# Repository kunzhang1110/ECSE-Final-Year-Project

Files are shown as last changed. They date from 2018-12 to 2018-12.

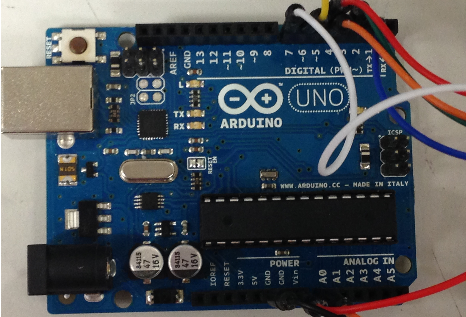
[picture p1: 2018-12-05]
Reports/Poster/Arduino.PNG

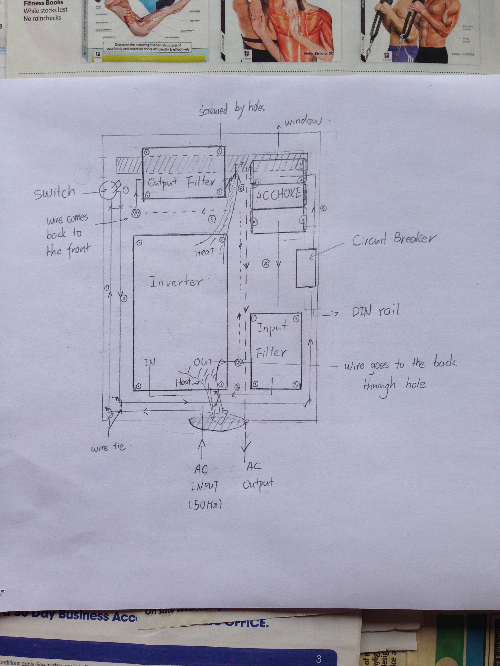
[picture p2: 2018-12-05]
Reports/Final Report/photo1.JPG

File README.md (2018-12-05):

# ECSE-Final-Year-Project
**Monash University**

*Semester 1 and 2, 2013*

## Description
The project is about designing a current-controlled AC-AC inverter and developing programs for controlling and setting this inverter. The inverter is used for motor control and other applications. The innovation of this project involves real-time controlling of the inverter parameters and the control methodology applied. The project also creates fast communication between the inverter and user’s terminals, such as a PC. 

## Environment
* Simulation: Matlab Simulink
* Implementation: Arduino and Atmel PWM controller(AT90PWM3B)
* PCB Board: Altium Designer

## Info
written by Kun Zhang (kunzhang1110@gmail.com)

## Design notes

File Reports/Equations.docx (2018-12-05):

# Power losses

The output current i of the PWM-inverter can be assumed to be sinusoidal with a peak value I_(peak)

i=I_(peak) cos(θ-φ)

where φ is the phase-angle difference between output voltage and current, θ is the phase angle of the voltage.

The conduction loss of one IGBT is

P_(con, 1) =(V_(FI) I_(peak))/(2π)∫_(-π/2+φ)^(π/2+φ) Dcos(θ-φ) dθ

where V_(FI) is the forward voltage of the IGBT and D is the duty cycle

The conduction loss of one bootstrapping diode is

P_(con, 2) =(V_(FD) I_(peak))/(2π)∫_(-π/2+φ)^(π/2+φ) (1-D)cos(θ-φ) dθ

where V_(FD) is the forward voltage of the bootstrapping diode

The duty cycle at a given θ can be obtained by

D=(V_P cosθ+0.5V_(DC))/(V_(DC))

where V_P is the peak of the output phase voltage and VDC is the DC link voltage

Eventually, the conduction losses is given by

P_(con) =P_(con, 1) +P_(con, 2) =(I_(peak))/(2π)(V_(FI) +V_(FD) )+(I_(peak) V_p)/(4V_(DC))(V_(FI) -V_(FD) )cosφ

Assume I_(peak) =20

The switching energy losses L of the IGBTs and diodes can be calculated using the linear equations

L=(E_(sw(on)) +E_(sw(off)) )×i

where, Eon is the switching loss (on) characteristic and Eoff is the switching loss (off) characteristic of the semiconducting devices.

The conduction loss of one IGBT and one diode is

P_(sw) =1/(2π)∫_(-π/2+φ)^(π/2+φ) (E_(sw(on)) +E_(sw(off)) )I_(peak) cos(θ-φ)f_(sw) dθ

where fsw is the switching frequency

By integration, we have

P_(sw) =((E_(sw(on)) +E_(sw(off)) )× f_(sw) I_(peak))/π

The values of the switching loss characteristics can be found in the datasheet

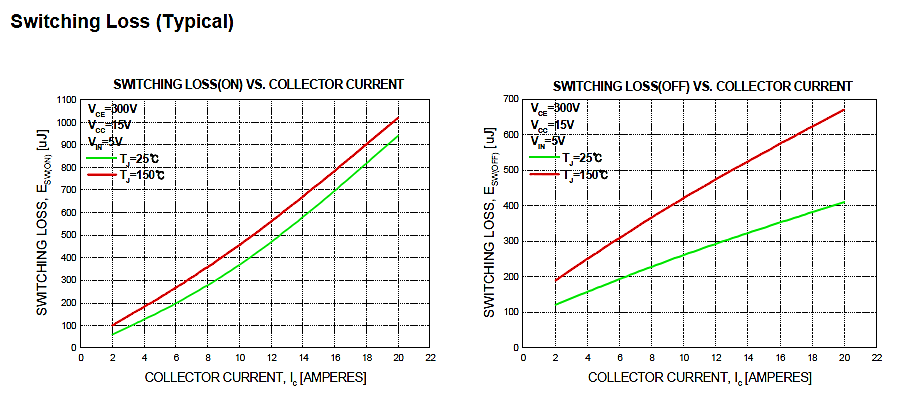
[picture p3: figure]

C=1/(2πfR)=1/(2π×400×18)=22 uF

f_(sw) =1/(t_(loop) *(Count_(Max) -1)+t_(loop_ADC))

where Count_Max is the maximum value of the counter

f_(sw) =1/(t_(loop) *Count_Max)

f_(sin) =f_(sw) *M/(NT)=M/(t_(loop) *Count_Max*NT)

Number of Table Values (NT)=f_(PWM) /f_(MODMAX)

θ=0.0032×108.7×360=125.2

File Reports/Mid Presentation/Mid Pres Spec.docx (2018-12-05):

Hi, my name is Kun Zhang. My final year project is intelligent power-electronics control. This project is an industry-based project, which is offered and supervised by Simplex CNC Systems.

The project is to design a current-controlled AC-AC inverter system which can be used for motor control and other applications. The innovation of the inverter involves real-time controlling of the inverter parameters and the control methodology applied. Also, filters are to be designed and utilised extensively to eliminate possible noises and harmonics.

I am going to talk about AC-AC Conversion methods first, and then I am going to introduce electric protection and filtration used in power electronics systems. Simulations have also been done to simulate the system I designed. At last, I am going to talk about the factory works I’ve been doing for the past seven weeks

Firstly, we need to choose an AC-AC conversion method for our inverter. Three common methods have been considered; they are cycloconverter, DC-link converter and matrix converter.

Cycloconverters synthesize the output waveform from segments of the AC supply. By controlling the switching patterns of the power switches, cycloconverters are able to convert an AC waveform to another AC waveform of a lower frequency. This puts a limit on the usage of cycloconverters as in our application, the frequency desired is 0~500 Hz with the input frequency of 50Hz. So, cycloconverters are not suitable for our design.

Next, lets consider DC-link converters. A DC-link converter converters AC from the mains to DC, and then inverters the DC to an AC with different frequencies. It consists of a rectifier at the supply side and an inverter (usually a voltage-controlled inverter) at the load side. The DC link shown in the middle is a large capacitor. It transmits the DC voltage to the inverter, preventing transients from flowing back to the input and provides some isolation from the utility line. The drawback of DC-link converters is they use large storage capacitors which have short lifetime and are bulky in size

A matrix converter has 9 bi-directional switches (18 transistors) that allow any output phase to be connected to any input phase. The input phases should never be short-circuited and the output currents should not be interrupted. This implies that one and only one bi-directional switch per output phase must be switched on at any instant. The primary advantage is that it reduces the harmonics significantly, hence less complicated filters are needed. However, the implementation and algorithms to control the switches are complex, and the cost is high.

Now, we can compare the three methods. As mentioned earlier, cycloconverters do not meet our frequency requirement, thus they’re not suitable for our design

Matrix converter is excellent insofar as it produces fewer harmonics and requires minimal capacitors and inductors. Yet, in terms of this project, it is not practical because it is too complex and too expensive.

DC-link converter is less efficient and contains considerable harmonics. However, DC-link converters are more feasible due to its low cost and high stability. Additionally, filters can be designed to reduce the harmonics. As a result, DC-link converter is the optimal choice for our application

To implement the conversion methods, we need to find a fitting power module first. A power module is a package of six power switching devices which are connected in bridge configurations. The requirements are shown in the table. The important thing is the switching frequency is 20~30 kilo Hz. This means BJTs cannot be used as they are too slow. GTO and power FETs are fast enough but they cannot stand 35A as required. So our choice is IGBT power modules.

Now, lets jump to electric protection. Electric protection is vital in electrical designs as it protects the system and its operators from faults.

A residual current device disconnects a circuit whenever it detects that the electric current is not balanced between the conductor and the return neutral conductor.

Type A RCDs which can detect full wave AC and pulsating DC residual currents.

Type B RCDs which can detect full wave AC, pulsating DC and pure DC residual

We prefer B as there will be DC current component involved in our application

A circuit breaker is a mechanical switching device, capable of making, carrying and breaking currents under normal circuit conditions.

Residual-current Circuit Breaker (RCCB) is the most common residual current device — detects current imbalance.

On top of that, a Residual current breaker with over-current protection (RCBO) protects the system from over-current. Overcurrent happens occasionally in motor applications, so RCBO is the best protection device in our design. Also, two RCBOs are connected in series, in case one fails

As DC-link converters contain considerable amount of noises, four filters are to be implemented in our design. An ac choke and input EMC filters for the input end and an output EMC filter with an output sine-wave filter for the output end. The total harmonic distortion is expected to be less than 5% for each end.

An ac choke is in essence an inductor which reduces harmonics from the mains. It also reduces commutation notches and limits inrush currents.

(Electromagnetic compatibility) EMC filters reduces the values of dv/dt, thus avoiding sharp changes. The dv/dt filters have cut-off frequency above the switching frequency. These filters also reduce the motor insulation stress. They are designed to be implemented at both input and output end.

Sine-wave filters provide a sinusoidal phase-to-phase motor voltage filtration. They have three effects: they reduce harmonics in the output; they reduce bearing current especially in large motors; Also, they reduce insulation stresses

The system I designed was simulated using Simulinks in MATLAB.

In brief, the DC-link inverter system consists of three blocks, a rectifier rectifies the mains, an inverter converts the DC to desired AC ---- which is fed to a motor. The simulation at this stage is done in open-loop. However, the system will be closed-loop controlled

The rectifier is constructed by six diodes with RC snubbers.

The AC source is configured in a way that it contains some harmonics, which is supposed to be filtered by the input EMC filter and input ac choke.

The rectification schematic also includes the DC-link section which contains an inductor with a large storage capacitor.

The first graph is the rectified voltage after the rectifier and the second graph is the voltage after DC link. It can be seen here that the stabilized output of the rectifier contains mainly DC with moderate distortions. These distortions are further reduced by DC-link.

The voltage is almost DC with a voltage of 150V

The motor simulation assumes the input of the inverter to be a well-rectified DC, which is modelled by a DC source. The three-phase PWM generator is set to generate a 100Hz modulation signal feeding into the inverter. The torque is fed back to the induction motor with a torque-speed characteristic as shown.

The first graph shows the rotor speed and the second graph shows the electromagnetic torque. It can be observed that the rotor speed is constant after 0.18s while the torque stabilizes after the same period of time. The rotor speed is around 180 rad/s (57Hz) because the slip of the induction motor was set to 0.5.

This is an industry-based project, so a considerable amount of works were done in factory. The factory works include assembling cabinets, wiring, device installation and assembling PCs. The cabinets are designed to hold the inverters and the filters. Rivets had to be punched into the metal plates first so that the they could assembled by screws. Once the cabinets were assembled, some model devices were installed in them. This was done by drilling holes to the metal plates of the cabinets and attached the model devices to the plate using's screws via those holes. Then, proper wiring paths were designed and the devices were wired accordingly. In addition, I also learnt and assembled a PC in the factory.

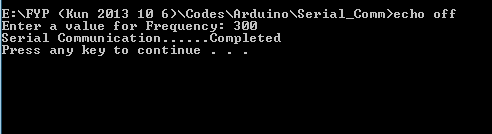
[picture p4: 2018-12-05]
Reports/Poster/BAT_Program.PNG

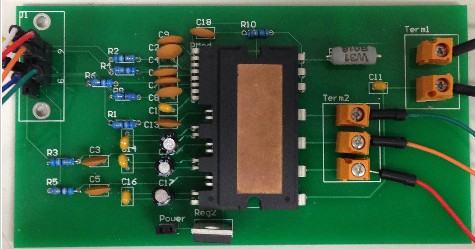
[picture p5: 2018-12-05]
Reports/Poster/PCBBoard.PNG

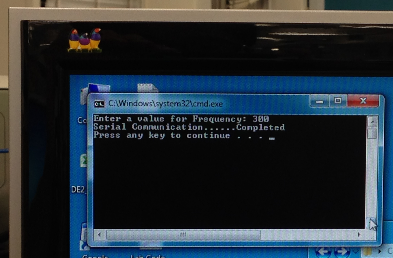
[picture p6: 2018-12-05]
Reports/Poster/PC_and_BAT.PNG

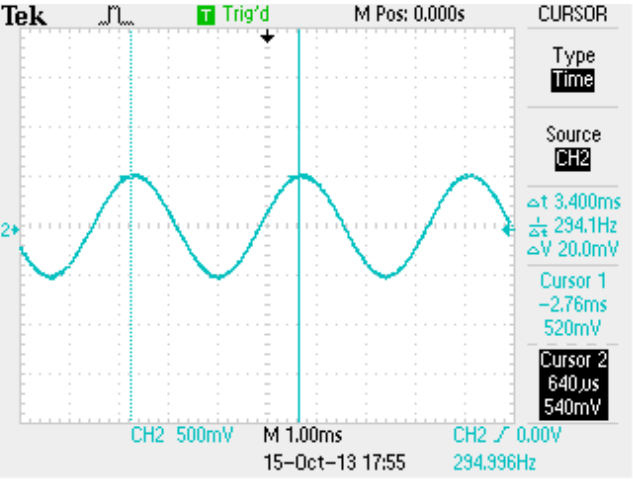
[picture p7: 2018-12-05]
Reports/Poster/AC.PNG

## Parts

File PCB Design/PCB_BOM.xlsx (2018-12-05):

Name | Qty | Unit Price | Total Price | Website/Store | Note
ACS71 Modules | 2 | 9.81 | 19.62 | http://www.ebay.com.au/itm/ACS712-Current-Sensor-Module-Detector-30-Amps-Amperage-Range-/300866546436
FSBB20CH60C | 1 | 14.73 | 14.73 | http://www.ebay.com.au/itm/1PCS-FSBB20CH60C-Smart-Power-Module-/321196353753?pt=LH_DefaultDomain_0
PCB Terminal Blocks, 2 pin | 5 | 2.33 | 2.33 | http://www.ebay.com.au/itm/5-Pcs-300V-PCB-Mount-Screw-Terminal-Blocks-20A-9-5mm-Pitch-/330839181034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
PCB Terminal Blocks, 3 pin | 5 | 5.07 | 5.07 | http://www.ebay.com.au/itm/5-Pcs-7-62mm-Pitch-3P-PCB-Screw-Terminal-Block-Black-20A-/390494651120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
0.018 Ohms resistor | 1 |  |  | http://au.element14.com/welwyn/w31-r018-ji/resistor-3w-5-0r018/dp/9497102
15 uF capacitor | 1 |  |  | http://au.element14.com/panasonic/eeaga1c150/capacitor-15uf-16v-4x7mm/dp/2079091
Headers | 10 |  | 1 | http://www.ebay.com.au/itm/10pcs-40-Pins-PCB-Panel-IC-2-54mm-Single-Row-Male-Header-Strip-DIY-Connector-New-/310573221650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
Jumper Wire | 40 |  | 2.83 | http://www.ebay.com.au/itm/40pcs-Female-to-Female-F-F-Dupont-Cable-Dupont-Wire-Color-Jumper-Fr-Arduino-20cm-/190818541015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
ISP Header 6-pin
ISP Wire 6-way

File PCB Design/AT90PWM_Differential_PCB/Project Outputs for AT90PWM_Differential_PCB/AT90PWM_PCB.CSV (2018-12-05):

Bill of Material for AT90PWM_PCB.PcbDoc
On 2013/9/2 星期一 at 22:09:55
Comment | Pattern | Quantity | Components
AT90PWM3 | AT90PWM3B | 1 | U1
Cap | NPolar_Cap | 2 | C1, C2 | Capacitor
Header 1 | HDR1X2 | 1 | P1 | Header, 2-Pin
Header 2 | HDR1X2 | 1 | P2 | Header, 2-Pin
Header 3 | HDR1X3 | 1 | P3 | Header, 3-Pin
Header 3X2 | HDR2X3 | 1 | P4 | Header, 3-Pin, Dual row
Header 5X2 | HDR2X5 | 1 | JTAG | Header, 5-Pin, Dual row

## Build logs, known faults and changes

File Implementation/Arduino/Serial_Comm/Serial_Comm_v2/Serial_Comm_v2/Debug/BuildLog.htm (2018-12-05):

Build Log

| | Build started: Project: Serial_Comm_v2, Configuration: Debug|Win32

Command Lines

Creating temporary file "g:\FYP (Kun 2013 10 6)\Codes\Arduino\Serial_Comm\Serial_Comm_v2\Serial_Comm_v2\Debug\RSP000001130083668.rsp" with contents
[
/Od /D "_MBCS" /Gm /EHsc /RTC1 /MDd /Fo"Debug\\" /Fd"Debug\vc90.pdb" /W3 /c /ZI /TC ".\Serial_COM_C.c"
]
Creating command line "cl.exe @"g:\FYP (Kun 2013 10 6)\Codes\Arduino\Serial_Comm\Serial_Comm_v2\Serial_Comm_v2\Debug\RSP000001130083668.rsp" /nologo /errorReport:prompt"
Creating temporary file "g:\FYP (Kun 2013 10 6)\Codes\Arduino\Serial_Comm\Serial_Comm_v2\Serial_Comm_v2\Debug\RSP000002130083668.rsp" with contents
[
/OUT:"G:\FYP (Kun 2013 10 6)\Codes\Arduino\Serial_Comm\Serial_Comm_v2\Debug\Serial_Comm_v2.exe" /MANIFEST /MANIFESTFILE:"Debug\Serial_Comm_v2.exe.intermediate.manifest" /MANIFESTUAC:"level='asInvoker' uiAccess='false'" /DEBUG /PDB:"g:\FYP (Kun 2013 10 6)\Codes\Arduino\Serial_Comm\Serial_Comm_v2\Debug\Serial_Comm_v2.pdb" /DYNAMICBASE /NXCOMPAT /MACHINE:X86 kernel32.lib user32.lib gdi32.lib winspool.lib comdlg32.lib advapi32.lib shell32.lib ole32.lib oleaut32.lib uuid.lib odbc32.lib odbccp32.lib

".\Debug\Serial_COM_C.obj"
]
Creating command line "link.exe @"g:\FYP (Kun 2013 10 6)\Codes\Arduino\Serial_Comm\Serial_Comm_v2\Serial_Comm_v2\Debug\RSP000002130083668.rsp" /NOLOGO /ERRORREPORT:PROMPT"
Creating temporary file "g:\FYP (Kun 2013 10 6)\Codes\Arduino\Serial_Comm\Serial_Comm_v2\Serial_Comm_v2\Debug\RSP000003130083668.rsp" with contents
[
/outputresource:"..\Debug\Serial_Comm_v2.exe;#1" /manifest

".\Debug\Serial_Comm_v2.exe.intermediate.manifest"
]
Creating command line "mt.exe @"g:\FYP (Kun 2013 10 6)\Codes\Arduino\Serial_Comm\Serial_Comm_v2\Serial_Comm_v2\Debug\RSP000003130083668.rsp" /nologo"
Creating temporary file "g:\FYP (Kun 2013 10 6)\Codes\Arduino\Serial_Comm\Serial_Comm_v2\Serial_Comm_v2\Debug\BAT000004130083668.bat" with contents
[
@echo Manifest resource last updated at %TIME% on %DATE% > ".\Debug\mt.dep"
]
Creating command line """g:\FYP (Kun 2013 10 6)\Codes\Arduino\Serial_Comm\Serial_Comm_v2\Serial_Comm_v2\Debug\BAT000004130083668.bat"""

Output Window

| | Compiling... Serial_COM_C.c g:\fyp (kun 2013 10 6)\codes\arduino\serial_comm\serial_comm_v2\serial_comm_v2\serial_com_c.c(4) : warning C4013: 'system' undefined; assuming extern returning int Linking... LINK : G:\FYP (Kun 2013 10 6)\Codes\Arduino\Serial_Comm\Serial_Comm_v2\Debug\Serial_Comm_v2.exe not found or not built by the last incremental link; performing full link Embedding manifest...

Results

| | Build log was saved at "file://g:\FYP (Kun 2013 10 6)\Codes\Arduino\Serial_Comm\Serial_Comm_v2\Serial_Comm_v2\Debug\BuildLog.htm" Serial_Comm_v2 - 0 error(s), 1 warning(s)

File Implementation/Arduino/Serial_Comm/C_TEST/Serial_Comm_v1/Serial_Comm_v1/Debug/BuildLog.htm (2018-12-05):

Build Log

| | Build started: Project: Serial_Comm_v1, Configuration: Debug|Win32

Command Lines

Creating temporary file "g:\FYP (Kun 2013 10 6)\Codes\Arduino\Serial_Comm\C_TEST\Serial_Comm_v1\Serial_Comm_v1\Debug\RSP000005100048716.rsp" with contents
[
/Od /D "_MBCS" /Gm /EHsc /RTC1 /MDd /Fo"Debug\\" /Fd"Debug\vc90.pdb" /W3 /c /ZI /TC ".\Serial_Comm_v1_C.c"
]
Creating command line "cl.exe @"g:\FYP (Kun 2013 10 6)\Codes\Arduino\Serial_Comm\C_TEST\Serial_Comm_v1\Serial_Comm_v1\Debug\RSP000005100048716.rsp" /nologo /errorReport:prompt"
Creating temporary file "g:\FYP (Kun 2013 10 6)\Codes\Arduino\Serial_Comm\C_TEST\Serial_Comm_v1\Serial_Comm_v1\Debug\RSP000006100048716.rsp" with contents
[
/OUT:"G:\FYP (Kun 2013 10 6)\Codes\Arduino\Serial_Comm\C_TEST\Serial_Comm_v1\Debug\Serial_Comm_v1.exe" /MANIFEST /MANIFESTFILE:"Debug\Serial_Comm_v1.exe.intermediate.manifest" /MANIFESTUAC:"level='asInvoker' uiAccess='false'" /DEBUG /PDB:"g:\FYP (Kun 2013 10 6)\Codes\Arduino\Serial_Comm\C_TEST\Serial_Comm_v1\Debug\Serial_Comm_v1.pdb" /DYNAMICBASE /NXCOMPAT /MACHINE:X86 kernel32.lib user32.lib gdi32.lib winspool.lib comdlg32.lib advapi32.lib shell32.lib ole32.lib oleaut32.lib uuid.lib odbc32.lib odbccp32.lib

".\Debug\Serial_Comm_v1_C.obj"
]
Creating command line "link.exe @"g:\FYP (Kun 2013 10 6)\Codes\Arduino\Serial_Comm\C_TEST\Serial_Comm_v1\Serial_Comm_v1\Debug\RSP000006100048716.rsp" /NOLOGO /ERRORREPORT:PROMPT"
Creating temporary file "g:\FYP (Kun 2013 10 6)\Codes\Arduino\Serial_Comm\C_TEST\Serial_Comm_v1\Serial_Comm_v1\Debug\RSP000007100048716.rsp" with contents
[
/outputresource:"..\Debug\Serial_Comm_v1.exe;#1" /manifest

".\Debug\Serial_Comm_v1.exe.intermediate.manifest"
]
Creating command line "mt.exe @"g:\FYP (Kun 2013 10 6)\Codes\Arduino\Serial_Comm\C_TEST\Serial_Comm_v1\Serial_Comm_v1\Debug\RSP000007100048716.rsp" /nologo"
Creating temporary file "g:\FYP (Kun 2013 10 6)\Codes\Arduino\Serial_Comm\C_TEST\Serial_Comm_v1\Serial_Comm_v1\Debug\BAT000008100048716.bat" with contents
[
@echo Manifest resource last updated at %TIME% on %DATE% > ".\Debug\mt.dep"
]
Creating command line """g:\FYP (Kun 2013 10 6)\Codes\Arduino\Serial_Comm\C_TEST\Serial_Comm_v1\Serial_Comm_v1\Debug\BAT000008100048716.bat"""

Output Window

| | Compiling... Serial_Comm_v1_C.c g:\fyp (kun 2013 10 6)\codes\arduino\serial_comm\c_test\serial_comm_v1\serial_comm_v1\serial_comm_v1_c.c(14) : warning C4047: '=' : 'int' differs in levels of indirection from 'char [4]' Linking... LINK : G:\FYP (Kun 2013 10 6)\Codes\Arduino\Serial_Comm\C_TEST\Serial_Comm_v1\Debug\Serial_Comm_v1.exe not found or not built by the last incremental link; performing full link Embedding manifest...

Results

| | Build log was saved at "file://g:\FYP (Kun 2013 10 6)\Codes\Arduino\Serial_Comm\C_TEST\Serial_Comm_v1\Serial_Comm_v1\Debug\BuildLog.htm" Serial_Comm_v1 - 0 error(s), 1 warning(s)

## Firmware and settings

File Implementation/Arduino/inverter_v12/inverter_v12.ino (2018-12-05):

#include <math.h>
/******************************************************************************************************/
/*    This code is to use preset reference signal freqeucies and generate PWM in open loop            */
/*    Version 12, based on SIMULINK code                                                               */
/*                                                                                                    */
/******************************************************************************************************/

//PWM pin numbers
int pwm_1_Pin= 8;                   
int pwm_2_Pin= 3;                   
int pwm_3_Pin= 4;                  
int pwm_4_Pin= 5;                   
int pwm_5_Pin= 6;                   
int pwm_6_Pin= 7;  

//Analogue pin number
int fdb_a_Pin= A0;                  //select A0,A1 for feedback signals
int fdb_b_Pin= A1;
//Frequencies of reference
int REF_FREQ= 300;                  //reference AC frequency

//initialize variables
double ref_a= 0;
double ref_b= 0;
double ref_c= 0;
int counter= 0;
double fb_a= 0;
double fb_b= 0;
int fb_c= 0;

//define constants
int counter_max= 1023;
int DEAD_TIME= 1;
int SINE_TABLE_MAX= 512;
int FEEDBACK_GAIN= 0;
int PROP_GAIN= 1;
double sin_table[512]={512,518,524,530,537,543,549,555,562,568,574,580,587,593,599,605,611,617,624,630,636,642,648,654,660,666,672,678,684,690,696,701,707,713,719,725,730,736,741,747,753,758,764,769,774,780,785,790,796,801,806,811,816,821,826,831,836,841,846,850,855,860,864,869,873,878,882,886,890,895,899,903,907,911,915,919,922,926,930,933,937,940,944,947,950,953,957,960,963,966,968,971,974,977,979,982,984,986,989,991,993,995,997,999,1001,1003,1004,1006,1008,1009,1011,1012,1013,1014,1015,1017,1017,1018,1019,1020,1021,1021,1022,1022,1022,1023,1023,1023,1023,1023,1023,1023,1022,1022,1022,1021,1021,1020,1019,1018,1017,1017,1015,1014,1013,1012,1011,1009,1008,1006,1004,1003,1001,999,997,995,993,991,989,986,984,982,979,977,974,971,968,966,963,960,957,953,950,947,944,940,937,933,930,926,922,919,915,911,907,903,899,895,890,886,882,878,873,869,864,860,855,850,846,841,836,831,826,821,816,811,806,801,796,790,785,780,774,769,764,758,753,747,741,736,730,725,719,713,707,701,696,690,684,678,672,666,660,654,648,642,636,630,624,617,611,605,599,593,587,580,574,568,562,555,549,543,537,530,524,518,512,505,499,493,486,480,474,468,461,455,449,443,436,430,424,418,412,406,399,393,387,381,375,369,363,357,351,345,339,333,327,322,316,310,304,298,293,287,282,276,270,265,259,254,249,243,238,233,227,222,217,212,207,202,197,192,187,182,177,173,168,163,159,154,150,145,141,137,133,128,124,120,116,112,108,104,101,97,93,90,86,83,79,76,73,70,66,63,60,57,55,52,49,46,44,41,39,37,34,32,30,28,26,24,22,20,19,17,15,14,12,11,10,9,8,6,6,5,4,3,2,2,1,1,1,0,0,0,0,0,0,0,1,1,1,2,2,3,4,5,6,6,8,9,10,11,12,14,15,17,19,20,22,24,26,28,30,32,34,37,39,41,44,46,49,52,55,57,60,63,66,70,73,76,79,83,86,90,93,97,101,104,108,112,116,120,124,128,133,137,141,145,150,154,159,163,168,173,177,182,187,192,197,202,207,212,217,222,227,233,238,243,249,254,259,265,270,276,282,287,293,298,304,310,316,322,327,333,339,345,351,357,363,369,375,381,387,393,399,406,412,418,424,430,436,443,449,455,461,468,474,480,486,493,499,505};
int i= 0;
int j= 13;
int n= 8;
/******************************************************************************************************/


void setup(){
  //declare outputs
  pinMode(pwm_1_Pin, OUTPUT);
  pinMode(pwm_2_Pin, OUTPUT);  
  pinMode(pwm_3_Pin, OUTPUT);  
  pinMode(pwm_4_Pin, OUTPUT);  
  pinMode(pwm_5_Pin, OUTPUT);  
  pinMode(pwm_6_Pin, OUTPUT);
  pinMode(13, OUTPUT);
  //declare inputs
  pinMode(fdb_a_Pin, INPUT);
  pinMode(fdb_b_Pin, INPUT);    
  ADCSRA=  0x84;                              //set ADC prescalar to 16; enable ADC conversion
  while(1){
      if(counter==counter_max){                                                  //if counter reaches maximum, take new values
             if(i==SINE_TABLE_MAX){
               i= 0;
             }else{
               i= i+n;
             } 
             if(j==SINE_TABLE_MAX){
               j= 0;
             }else{
               j= j+n;
             }            
             ref_a= sin_table[i];                                     //set ref_phase to a scale of 0 to COUNT_MAX
         ref_b= sin_table[j];
             ref_c= (-ref_a-ref_b)+(counter_max)*3/2;
//                          fb_a=analogRead(fdb_a_Pin);    //feedback ranging from 0-1023
//             fb_b=analogRead(fdb_b_Pin);
//    fb_c= -fb_a-fb_b;  
//                ref_a= (ref_a-fb_a*FEEDBACK_GAIN)*PROP_GAIN;  
//                
//    ref_b= (ref_b-fb_b*FEEDBACK_GAIN)*PROP_GAIN;
//    ref_c= (ref_c-fb_c*FEEDBACK_GAIN)*PROP_GAIN;
             counter= 0;             //reset counter

 }

   if(counter<DEAD_TIME){                                                   //initially, pwm 1->0, delay for 5 ticks (at the rate of Timer2)   
               PORTB = 0;
               PORTD = 0;
   }else{
       //leg 1
       if(counter<ref_a){
              PORTB &= ~0x01;      PORTD |= 0x08;
       }else if(counter<ref_a+DEAD_TIME*50){
              PORTB &= ~0x01;      PORTD &= ~0x08;
       }else{
              PORTB |= 0x01;       PORTD &= ~0x08;   
       }
   
    //leg 2
       if(counter<ref_b){
              PORTD &= ~0x10;      PORTD |= 0x20;
       }else if(counter<ref_b+DEAD_TIME*50){
              PORTD &= ~0x10;      PORTD &= ~0x20;
       }else{
              PORTD |= 0x10;       PORTD &= ~0x20;      
       }
 
    //leg 3
       if(counter<ref_c){
              PORTD &= ~0x40;     PORTD |= 0x80; 
       }else if(counter<ref_c+DEAD_TIME*50){
              PORTD &= ~0x40;     PORTD &= ~0x80;
       }else{
              PORTD |= 0x40;      PORTD &= ~0x80;   
       }  
   }
   counter= counter+100;       //counter increments
  }
}  


/*****************************************************************************************************/
void loop() {    
}   
//Each while loop: 11.9KHz

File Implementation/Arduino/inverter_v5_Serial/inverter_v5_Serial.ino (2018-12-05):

#include <math.h>
/******************************************************************************************************/
/*    This code is to use preset reference signal freqeucies and generate PWM in open loop            */
/*    Version 5, based on SIMULINK code                                                               */
/*                                                                                                    */
/******************************************************************************************************/

//PWM pin numbers
int pwm_1_Pin= 8;                   
int pwm_2_Pin= 3;                   
int pwm_3_Pin= 4;                  
int pwm_4_Pin= 5;                   
int pwm_5_Pin= 6;                   
int pwm_6_Pin= 7;                   

//Analogue pin number
int fdb_a_Pin= A0;                  //select A0,A1 for feedback signals
int fdb_b_Pin= A1;
//Frequencies of reference
int REF_FREQ= 80;                  //reference AC frequency
byte byteRead [3]= {48,56};
//initialize variables
double ref_a= 0;
double ref_b= 0;
double ref_c= 0;
int counter= 0;
double fb_a= 0;
double fb_b= 0;
int counter_max= 4;
int n= 1;
//define constants
int sem_1= 0;
int sem_2= 0;
int sem_3= 0;
int DEAD_TIME= 1;
int SINE_TABLE_MAX= 20;
double sin_table[21]={5.00, 6.55, 7.94, 9.05, 9.76, 10.00,9.76, 9.05, 7.94, 6.55, 5.00,3.45, 2.06, 0.95, 0.24, 0.00, 0.245, 0.95, 2.06, 3.45, 5.00};
int i= 0;
int j= 6;
/******************************************************************************************************/

void setup(){
  //declare outputs
  pinMode(pwm_1_Pin, OUTPUT);
  pinMode(pwm_2_Pin, OUTPUT);  
  pinMode(pwm_3_Pin, OUTPUT);  
  pinMode(pwm_4_Pin, OUTPUT);  
  pinMode(pwm_5_Pin, OUTPUT);  
  pinMode(pwm_6_Pin, OUTPUT);
  //declare inputs
  pinMode(fdb_a_Pin, INPUT);
  pinMode(fdb_b_Pin, INPUT);  
  ADCSRA=  0x84;                              //set ADC prescalar to 16; enable ADC conversion
  Serial.begin(115200);
  while(1){
 
    if(counter==counter_max){ 
      if (Serial.available()){
        byteRead[0] = Serial.read();  
        byteRead[1] = Serial.read(); 
        //      byteRead[2] = Serial.read(); 
        if(byteRead[0]<255&&byteRead[1]<255){
          n=(byteRead[0]-48)*10+(byteRead[1]-48);  
        }
           Serial.println(n);
      }
      //if counter reaches maximum, take new values
      if(i==SINE_TABLE_MAX){
        i= 0;
      }
      else{
        i= i+n;
      } 
      if(j==SINE_TABLE_MAX){
        j= 0;
      }
      else{
        j= j+n;
      }            
      ref_a= sin_table[i];                                     //set ref_phase to a scale of 0 to COUNT_MAX
      ref_b= sin_table[j];
      ref_c= (-ref_a-ref_b)+15;
      counter= 0;             //reset counter
      sem_1= 0;
      sem_2= 0;
      sem_3= 0;
      fb_a=analogRead(fdb_a_Pin);
      fb_b=analogRead(fdb_b_Pin);
    }

    if(counter==0){                                                   //initially, pwm 1->0, delay for 5 ticks (at the rate of Timer2)   
      //             PORTD &= ~0x4;       PORTD &= ~0x8;              
      //             PORTD &= ~0x10;      PORTD &= ~0x20;
      //             PORTD &= ~0x40;      PORTD &= ~0x80;
      delayMicroseconds(3);
      PORTD= 0;
      PORTB= 0;
      //             delayMicroseconds(1);                                          //balance computation time
    }
    else{
      //leg 1
      if(counter<ref_a){
        PORTB &= ~0x01;     
        PORTD |= 0x08;
      }
      else if(sem_1==0) {
        PORTB &= ~0x01;      
        PORTD &= ~0x08;
        delayMicroseconds(1);
        PORTB |= 0x01;       
        PORTD &= ~0x08; 
        sem_1= 1;  
      }
      else{
        PORTB |= 0x01;       
        PORTD &= ~0x08;         
      } 

      //leg 2
      if(counter<ref_b){
        PORTD &= ~0x10;      
        PORTD |= 0x20;
      }
      else if(counter<ref_b+DEAD_TIME){
        PORTD &= ~0x10;      
        PORTD &= ~0x20;
      }
      else{
        PORTD |= 0x10;       
        PORTD &= ~0x20;      
      }

      //leg 3
      if(counter<ref_c){
        PORTD &= ~0x40;     
        PORTD |= 0x80; 
      }
      else if(counter<ref_c+DEAD_TIME){
        PORTD &= ~0x40;     
        PORTD &= ~0x80;
      }
      else{
        PORTD |= 0x40;      
        PORTD &= ~0x80;   
      }  
    }
    counter= counter+1;       //counter increments
  }
}  


/*****************************************************************************************************/
void loop() {    
}   
